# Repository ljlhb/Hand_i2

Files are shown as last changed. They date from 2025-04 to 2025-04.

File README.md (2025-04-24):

## 手i2

从图库下载 STL 文件：i2RightHand i2LeftHand。

在打印所有部件之前，您应该打印一份校准器 (CALIBRATOR)，以检查部件是否能够拼合。如果您在拼合这些部件时遇到困难，可以调整切片软件的水平扩展设置来解决这个问题。此设置可能因切片机和打印机而异，但用户报告称，将其设置为 -0.15 是一个不错的起点。

以下是一只右手所需的零件清单和打印数量：

1个i2_CoverFingerV3
1x i2_FingersMoldX5V3
1个 i2_FingersTipX5V2
1个i2_FingersX5V1
1x i2_HandCoverV1
1个i2_PalmCoverV2
1x i2_PulleyX5V1
1x i2_WristGearV1
1个 i2_WristLargeV2
打印腕部大件、手指模具、手指、腕带、滑轮，最大分辨率 0.25，填充率为 30%，壁厚为 2 毫米，无支撑，无筏。

打印 CoverFinger、FingersTip、HandCover、PalmCover，最大分辨率 0.25，填充率为 30%，壁厚为 2 毫米，需要支撑，如果打印机需要，则需要筏。

物料清单：

25个沉头螺钉M3 x 16mm
5 个 M3 x 4mm 沉头螺钉
1 个 M3 x 12mm 沉头螺钉
5 个平头螺钉 M1.5 x 4mm
5个膨胀弹簧3/16英寸x1-3/4或4.8毫米x44.5毫米
6x舵机 JX-6225MG 300度
1x 带状线 16 根 3 米
1 条编织鱼线 0.8 毫米 200 磅，3 米
5个霍尔传感器AH3503
5x 圆盘磁铁直径 2.5mmx1mm
1x 特氟龙管 ID1.5MM X OD2.5MM，3米

<h2>步骤1</h2>



将腕部伺服支架粘到 RobCableFront 上



用 4 个螺钉安装伺服电机



如果需要，用 M3 钻头重新钻孔



重新钻孔，以便 M3 PTFE 管穿过它们



使用 M3 钻头重新钻孔



将两个轴打印部件粘合在一起



检查以确保轴正确安装在两个印刷齿轮中



将 RobCableFront 和伺服支架安装到伺服床上



此视图向您展示了 WristGear 的组装以及各个部件如何组合在一起



将舵机角度设置为大约 90 度（HK15298B）或 150 度（JX-6225MG）。（即舵机总角度的中间值）。您可以使用此脚本(见脚本.txt)进行设置。用 3 毫米螺钉将组件末端安装到舵机轴上。



用 4 颗螺丝将组件拧到手腕上



按图示组装主齿轮



注意小齿轮的头部必须适合 RotaWrist2 的预留孔



使用 M3 螺丝刀将主齿轮与 RotaWrist3 对齐，然后添加 M3 x 12 毫米螺钉将它们固定在一起



删除那块打印的预支撑，你不再需要它了



用锋利的刀片，必要时清理边缘





使用 M8 钻头重新钻孔 WristLarge



使用 M3 丝锥，在将要固定手盖的地方准备一些 M3 x 16 毫米螺丝孔



使用 M3 丝锥，为安装弹簧的 M3 x 16 毫米螺钉准备孔



使用 M3 钻头，清理连接每个手指的所有孔



用M3钻头，将所有手指每3节的孔全部清理干净



用锋利的刀片清理霍尔传感器的出口



使用 M1.5 钻头，清理弹簧末端连接的孔



用填充物时，确保每个手指的三个部分都贴合，并且移动起来非常顺畅。这对于手指的良好功能至关重要。





使用 M5.5 钻头清理手指部分，让弹簧正常穿过



使用 M5.5 钻头清理手指部分，让弹簧正常穿过



这是为了向您展示如何将弹簧和三根传感器线安装在每个手指部分



确保针头可以穿过每个手指部分，如图所示，否则清理孔



使用 M3 x 16 毫米螺钉和螺栓将手指部分添加并安装在一起



确保编织鱼线的入口也清理干净



准备 5 条长度为 50 厘米的编织鱼线（0.8 毫米 200 磅）如果您在谷歌搜索中输入这些关键词，就可以找到该产品：编织鱼线 0.8 毫米 200 磅



准备一条40厘米长的带状电缆。你可以在谷歌搜索关键词：带状电缆 16 针（尽量选择最柔软、最细的）。



将丝带分成两部分，一部分长 40 厘米，有 6 根电线，另一部分长 10 根电线



从10根电线中完全移除1根电线。将9根电线分成三段，每段3根电线，长度均为15厘米。



用红色记号笔，给每个部分的一根电线涂上颜色。我们假设这些是正极 (+) 线



在丝带的两端都涂上这些颜色，这对于避免在进行最后的焊接时混合电线非常有用。



穿过腕部大号每 5 个丝带部分



将丝带穿过每个手指，注意不要倒着穿。另外要注意，每个手指的形状都差不多，只有拇指的形状不同。



现在把编织好的鱼线穿过每个手指。为了让鱼线末端更硬，可以加一些强力胶。



在 1 厘米长的编织钓鱼线上涂上强力胶。



等到它完全干燥后，从中间切开粘合部分，这样可以确保尖端坚固而纤薄。



通过将钓鱼线拉入指尖的 V 形凹槽，即可将其固定



现在将鱼线的另一端插入手腕大孔中



这是给你展示一下它应该是什么样子。我的照片上还没做拇指，不过你可以做。五个手指可以同时做。



如果你还没有这样做，请清理 3 毫米螺栓外壳，以便进行下一步



现在是时候添加 M3 x 16 毫米螺钉及其相应的螺栓，将手指组装到大腕上。从大拇指开始，然后是食指、无名指、小指，最后是拇指。



使用合适的 M8 印刷螺栓将 WristLarge 安装到 RotaWrist3



将微型夹具设置在打印螺栓的凹槽上



穿过主齿轮的最大丝带



然后穿过主齿轮第二条丝带



放置掌上盖并用 3 颗 M3 x 16 毫米螺钉固定



拧紧掌上盖时，确保将丝带整齐地放入凹槽中，并真正避免夹住它们



现在将 M2.5 PTFE 管穿过主齿轮特氟隆管 ID1.5MM X OD2.5MM PTFE 管的长度如下：拇指 335mm 食指 300mm 中间 300mm 无名指 300mm 小指 360mm

特氟隆管 ID1.5MM X OD2.5MM：https://fr.aliexpress.com/item/32730855848.html?spm=a2g0s.9042311.0.0.3b966c37jungcW



将管子穿过伺服底座孔。管子距离伺服轴约 1.5 厘米。



将鱼线穿过管子





并将管子的末端放入预留的孔中，直到无法再插入为止



对每根手指重复操作



现在获得 5 个弹簧弹簧 3/16″x1-3/4

弹簧 3/16″x1-3/4：https://www.ebay.com/p/19011685359



将一根鱼线穿过弹簧的一侧。鱼线总长度约为30厘米



将鱼线穿过主指部分的弹簧孔



将弹簧穿过第二个手指部分



取 5 个小螺丝，我用了一些安装在眼部机构中的伺服器上的螺丝，这些螺丝的直径约为 2 毫米





用钳子将螺丝剪至最大总长度为 4 毫米



将弹簧固定到位



装上那个小螺丝，把弹簧固定到位。确保螺丝没有刺穿三根带状电线



获取或切割五颗 3 毫米、最大长度为 4 毫米的螺钉



拉动鱼线，将弹簧头固定到位，然后安装螺丝。注意，我在螺丝刀上放了一块黑色磁铁，这样可以方便安装螺丝。



拧紧螺丝之前，先将鱼线拉出来



完成拧紧。确保没有刺穿三根带状电线



拿两根针



将手指的最后一部分最大限度地折叠起来，并将第一根针穿过手指和弹簧，直到它从另一侧出来。



折叠手指的第二节，并将第二根针穿过手指和弹簧，直至完全穿过。这样可以为每个手指节设置合适的张力。



用小钳子剪断针头



滴一滴强力胶，确保针头不会再出来



是时候用拇指做同样的事情了，只有两个手指部分，所以弹簧的张力较小，不需要针



拇指的另一个不同之处在于，我们将螺丝拧入盖子中，从而将弹簧固定到位。确保不要刺穿电线。虽然我的图片显示已经装好了拇指盖，但先不要装上，你仍然需要接触到内部。



让我们把霍尔传感器焊接到电线上。开始焊接中间的电线。注意传感器在图片上的位置，因为一侧是正极，另一侧是负极。霍尔传感器 AH3503

霍尔传感器 AH3503：https://fr.aliexpress.com/item/32899671134.html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





用一小块胶带保护焊锡。我用的是Kapton胶带。这部分操作比较精细。



焊接第二根和第三根电线并用胶带包裹起来



缠绕胶带时，胶带的厚度不应超过丝带本身的厚度，否则下一步将其推下去会很困难。



小心地将其推回指尖



这是指尖应该伸出的长度



你可以拉动手掌中的电线，帮助自己将霍尔传感器推回到尖端



将钓鱼线缠绕在凹槽周围，然后小心地将手指末端拧到传感器上。



注意，手指末端印有小螺纹，可以顺时针旋转至指尖。请勿用力过猛，否则螺纹会损坏。



完成每个手指的操作。



你可以用一些 16x3mm 的螺丝安装手指盖。虽然我的图片显示手指盖已经装好了，但先不要装，你仍然需要打开内部。



是时候把每根线焊接到 NervoBoard 的传感器板上了。拇指放在“0”上，食指放在“1”上，大拇指放在“2”上，无名指放在“3”上，小指放在“4”上。



您可以在此页面上查看有关传感器连接的更多信息：https://inmoov.fr/test-your-finger-sensor/



这里你可以看到我放置迷你模拟板的位置。你还可以在滑轮上看到，带小垫圈的螺丝是如何将鱼线用一个结固定住的。要做到这一点，你需要在你想要剪断鱼线的地方涂上一些胶水。



要做到这一点，你需要在你想要剪断的编织线上涂点胶水，让接触胶固化。胶水可以让剪断更容易。



然后，用锋利的剪刀剪掉涂有胶水的地方。



按照我在图中的方式拉动你的钓鱼线，它应该会形成一个大结。



拧紧结，将螺钉和垫圈放在结上，并在拧紧螺钉时保持结被拉住。



模具中有一个孔，用于插入直径为2毫米的部件，以便在模制硅胶中形成一个复位，以便磁铁复位。圆盘磁铁直径为2.5毫米x1毫米。

圆盘磁铁直径为2.5毫米x1毫米：https://www.supermagnete.fr/eng/disc-magnets-neodymium/disc-magnet-2.5mm-1mm_S-2.5-01-N52N



让它穿过2毫米。我使用了双组分透明RTV硅胶Ecoflex™ 00-10



用硅胶套件将每个指尖上的模制部件粘合起来



用指南针确定磁铁的南极。



将磁铁的南极朝向霍尔传感器，插入硅胶模制尖端的复位孔中。请使用木质牙签，因为任何金属工具都会粘在磁铁上。这项工作很精细，必须操作到位才能获得正确的结果。用一滴硅胶套装固定磁铁位置，并等待其干燥。使用此页面https://inmoov.fr/test-your-finger-sensor/测试您的传感器。

## 如何使用手指传感器

手指传感器可以用于各种功能。抓取鸡蛋或瓶子需要不同的压力。握手也需要检测施加的压力。触摸传感器有很多种实现方法，我做过两个版本，成本都非常低。带霍尔传感器的版本比原来的泡沫版本精确得多。

概括：

电子版（2 个版本）
设置
利用率

**带霍尔传感器的电子装置**

-此版本采用霍尔传感器和磁铁完成。

-当磁铁靠近霍尔传感器时，传感器会测量该值。

-该值被发送到模拟 Arduino 引脚。

-手部教程中解释了手指上传感器的组装。







**电子泡沫传感器**

- 手指传感器的原始版本是用 2 块铜板连接到一块防静电泡沫制成的。

-当泡沫被压缩时，两块铜板之间的电流流动更强。

-模拟 Arduino 引脚检测变化。

-手部教程中解释了手指上传感器的组装。





**设置**

打开 InMoov/config/ service_J_SensorFinger.config并进行如下设置。

[MAIN]

rightHandSensorActivated=True
rightHandSensorArduino=right

right_thumb_Psi_min=544当传感器未按下时，请在此处输入最大值。
right_thumb_Psi_low=545一般情况下，取最小值，如果使用 AH3503 霍尔传感器，则加 1。
right_thumb_Psi_mid=547一般情况下，取最小值，加 4。
right_thumb_Psi_max=550一般情况下，取最小值，加 7。

right_index_Psi_min=538
right_index_Psi_low=539
right_index_Psi_mid=542
right_index_Psi_max=545

添加每个手指传感器的值……

要检查手指传感器是否工作正常并查看其值，您可以在 Python 窗口中输入并执行：

sensorTimerStart()

并在 python 选项卡中查看结果。

您可以使用以下方法关闭传感器定时器：

sensorTimerStop()

**利用率**

<h2>我们有三个选择：</h2>

1-如果您已经设置了传感器配置文件，某些手势将自动使用传感器。

2-直接在 Arduino 上使用代码进行测试。

3-使用 MyRobotLab 中的 Python 代码进行测试。（如果您没有运行 START_INMOOV）

<h3>第一个选项：</h3>

shakehands()当手闭合时，手势将自动使用传感器。

您可以将手势所需的压力调整为 0 到 3 之间的值。当传感器达到所需压力时，手指伺服器将停止其位置并禁用。

if rightHandSensorActivated:
    rightHandSensorON()
    sleep(1.5)
    rightThumbPressure=1 # Pressure range between 0-3
    rightIndexPressure=1
    rightMajeurePressure=1
    rightRingFingerPressure=1
    rightPinkyPressure=1
    i01.rightHand.moveTo(79,170,180,180,180,180)
    sleep(2)
    rightHandSensorOFF()
else:
  i01.rightHand.moveTo(79,90,140,130,122,180)

<h3>第二种选择：</h3>

-将此代码上传到您的 Arduino 板：

// A small script to test one servo and one sensor.

// Connect one sensor cable to the PIN A0, and the other cable
// to the 5V of your Arduino.
// The servo will be connected to your power supply (Gnd,Vcc)
// and to the PIN 2 of your Arduino.
// Set the serial of your Arduino at 57600 in device manager
// More detail on connection here https://inmoov.fr/test-your-finger-sensor
    
#include <Servo.h>

const int servoPin = 2;
const int sensorPin = A0;
int sensorReading;

int position;

Servo myservo;

void setup(){
  Serial.begin(57600);
  myservo.write(30);  // Closed claw.
  position = 30;
  myservo.attach(servoPin );
}

void loop(){
  sensorReading = analogRead(sensorPin);
    Serial.print("Analog reading = ");
    Serial.print(sensorReading); // the raw analog reading
    // We'll have a few threshholds, qualitatively determined
    if (sensorReading < 25) {
    Serial.println(" - No pressure");
    } else if (sensorReading < 30) {
    Serial.println(" - Light touch");
    } else if (sensorReading < 50) {
    Serial.println(" - Light squeeze");
    } else if (sensorReading < 110) {
    Serial.println(" - Medium squeeze");
    } else if (sensorReading < 200) {
    Serial.println(" - Big squeeze");
    }
    delay(1000);
  openClaw();
  delay(3000);
  closeClaw();
  delay(3000);
}

void openClaw() {
  for (; position < 130;  position++) {
    myservo.write(position);
    if(analogRead(sensorPin) > 30)
      break;
  }
}

void closeClaw() {
  myservo.write(30);  // Go to open position
  position = 30;
}

- 连接传感器（以 FSR 传感器为例）和伺服电机。有些伺服电机需要的电流过大，无法直接由 Arduino 供电。如果您的伺服电机抖动或运动不稳定，请为伺服电机连接一个额外的电源，并确保将 Arduino 连接到该额外的电源，如下所示：



-当通电时，手指会自动缓慢闭合，如果传感器检测到压力，则会在 Arduino.exe 监视器中显示信息。

-您可能需要更改代码中的传感器值以达到更好的调整。

为此，请检查监视器上的结果并根据需要直接在代码中更改这些值：

(sensorReading < 25)
(sensorReading < 30)
(sensorReading < 50)
(sensorReading < 110)
(sensorReading < 200)

<h3>第三种选择：</h3>

这里我们假设您已经安装了 MyRobotLab 并且知道如何使用它，如果没有，请先转到此页面。

-双击 MRL 目录中的“myrobotlab.jar”启动 MyRobotLab。

-按照第一个选项教程中的图像，在 Arduino 和伺服电机之间建立相同的连接。

-将此 python 脚本复制并粘贴到 MyRobotLab 中的 python 选项卡。

#这个简单的传感器 InMoov 脚本在 MyRobotLab 版本 1.0.2693 上进行了测试
#可以通过 Oscope 和手指动作看到结果。
#将一根传感器电缆连接到 PIN A0，将另一根电缆连接到 Arduino 的 5V。
#Servo 将连接到 Arduino 的引脚 2。
#根据您的Arduino板更改代码中的COM端口。

leftPort = "COM10"

Voice="US-English_Matthew"
mouth = Runtime.createAndStart("i01.mouth", "NaturalReaderSpeech")
#mouth.installComponentsAcceptLicense(Voice)
mouth.setVoice(Voice)
mouth.setRate(-10)

i01 = Runtime.createAndStart("i01", "InMoov")
i01.startMouth()
leftHand = Runtime.create("i01.leftHand","InMoovHand")
i01.startLeftHand(leftPort)
i01.leftHand.index.map(0,180,25,165)

left=Runtime.create("i01.left", "Arduino")
left.setBoard("atmega2560")
left = Runtime.start("i01.left", "Arduino")
left.connect("COM10")

def publishPin(pins): 
    for pin in range(0, len(pins)):
        print pins[pin].address, pins[pin].value
        if pins[pin].value<=540:
          print "No pressure"
        if pins[pin].value>=541 and pins[pin].value<=542:
          print "Low pressure"
        if pins[pin].value>=543 and pins[pin].value<=544:
          print "Soft pressure"
          FingerGoesBack()
        if pins[pin].value>=545:
          print "High pressure"
          FingerGoesBack()
          i01.mouth.speak(u"OUCH, that hurts") 
 
left.addListener("publishPinArray","python","publishPin")
sleep(5)
left.enablePin(54,1) # 54 is pin A0, Number 1 is how many polls/second

i01.leftHand.setAutoDisable(True)

def moveFingerSlowly():
    i01.leftHand.index.enable()
    i01.leftHand.index.setVelocity(25)
    sleep(2)
    i01.leftHand.index.moveTo(180)

def FingerGoesBack():
    i01.leftHand.index.enable()
    i01.leftHand.index.setVelocity(-1)
    i01.leftHand.index.moveTo(0)
 
#此简单的 InMoov 传感器脚本已在 MyRobotLab 1.1.812 版本上测试。
#结果可在 Oscope 中通过手指动作查看。
#将一根传感器线缆连接到 Arduino 的 A0 引脚，另一根线缆连接到 Arduino 的 5V 接口。
#伺服器将连接到 Arduino 的 2 引脚。
#根据您的 Arduino 开发板更改代码中的 COM 端口。

Voice="Mark" 
i01_mouth = Runtime.start("i01.mouth", "MarySpeech") 
#i01_mouth.installComponentsAcceptLicense(Voice) 
i01_mouth.setVoice(Voice) 

i01_left=Runtime.create("i01.left", "Arduino") 
i01_left.setBoard("atmega2560") 
i01_left = Runtime.start("i01.left", "Arduino") 
i01_left.connect("COM3") 

i01 = Runtime.start("i01", "InMoov2") 
i01.startMouth() 
i01_leftHand = Runtime.start("i01.leftHand","InMoov2Hand") 
i01_leftHand_index.map(0.0,180.0,0.0,180.0) 
i01_left.attach("i01.leftHand") 

def publishPin(pins):
    对于范围内的引脚（0，len（pins））：
        打印 pins[pin].address，pins[pin].value
        如果 pins[pin].value<=540：
          打印“无压力”
        如果 pins[pin].value>=541 且 pins[pin].value<=542：
          打印“低压”
        如果 pins[pin].value>=543 且 pins[pin].value<=544：
          打印“轻压” 
          FingerGoesBack()
        如果 pins[pin].value>=545：
          打印“高压” 
          FingerGoesBack() 
          i01.mouth.speak(u“哎哟，好疼”）
 
i01_left.addListener("publishPinArray","python","publishPin") 
sleep(5) 
i01_left.enablePin(54,1) # 54 是引脚 A0，数字 1 是每秒轮询次数

i01_leftHand.setAutoDisable(True) 

def moveFingerSlowly（）：
    i01_leftHand_index.enable（）
    i01_leftHand_index.setSpeed（25）
    睡眠（2）
    i01_leftHand_index.moveTo（180）

def FingerGoesBack（）：
    i01_leftHand_index.enable（）
    i01_leftHand_index.setSpeedy（250）
    i01_leftHand_index.moveTo（0）

-当通电时，手指会自动缓慢闭合，如果传感器检测到压力，它会在 Python 监视器中显示信息，并停止闭合并说出与他感受到的压力相关的内容。

-您可能需要更改代码中的传感器值以达到更好的调整。

为此，请检查监视器上的结果并根据需要直接在代码中更改这些值：

value<=540
value>=541
value<=542
value>=543
value<=544
value>=545

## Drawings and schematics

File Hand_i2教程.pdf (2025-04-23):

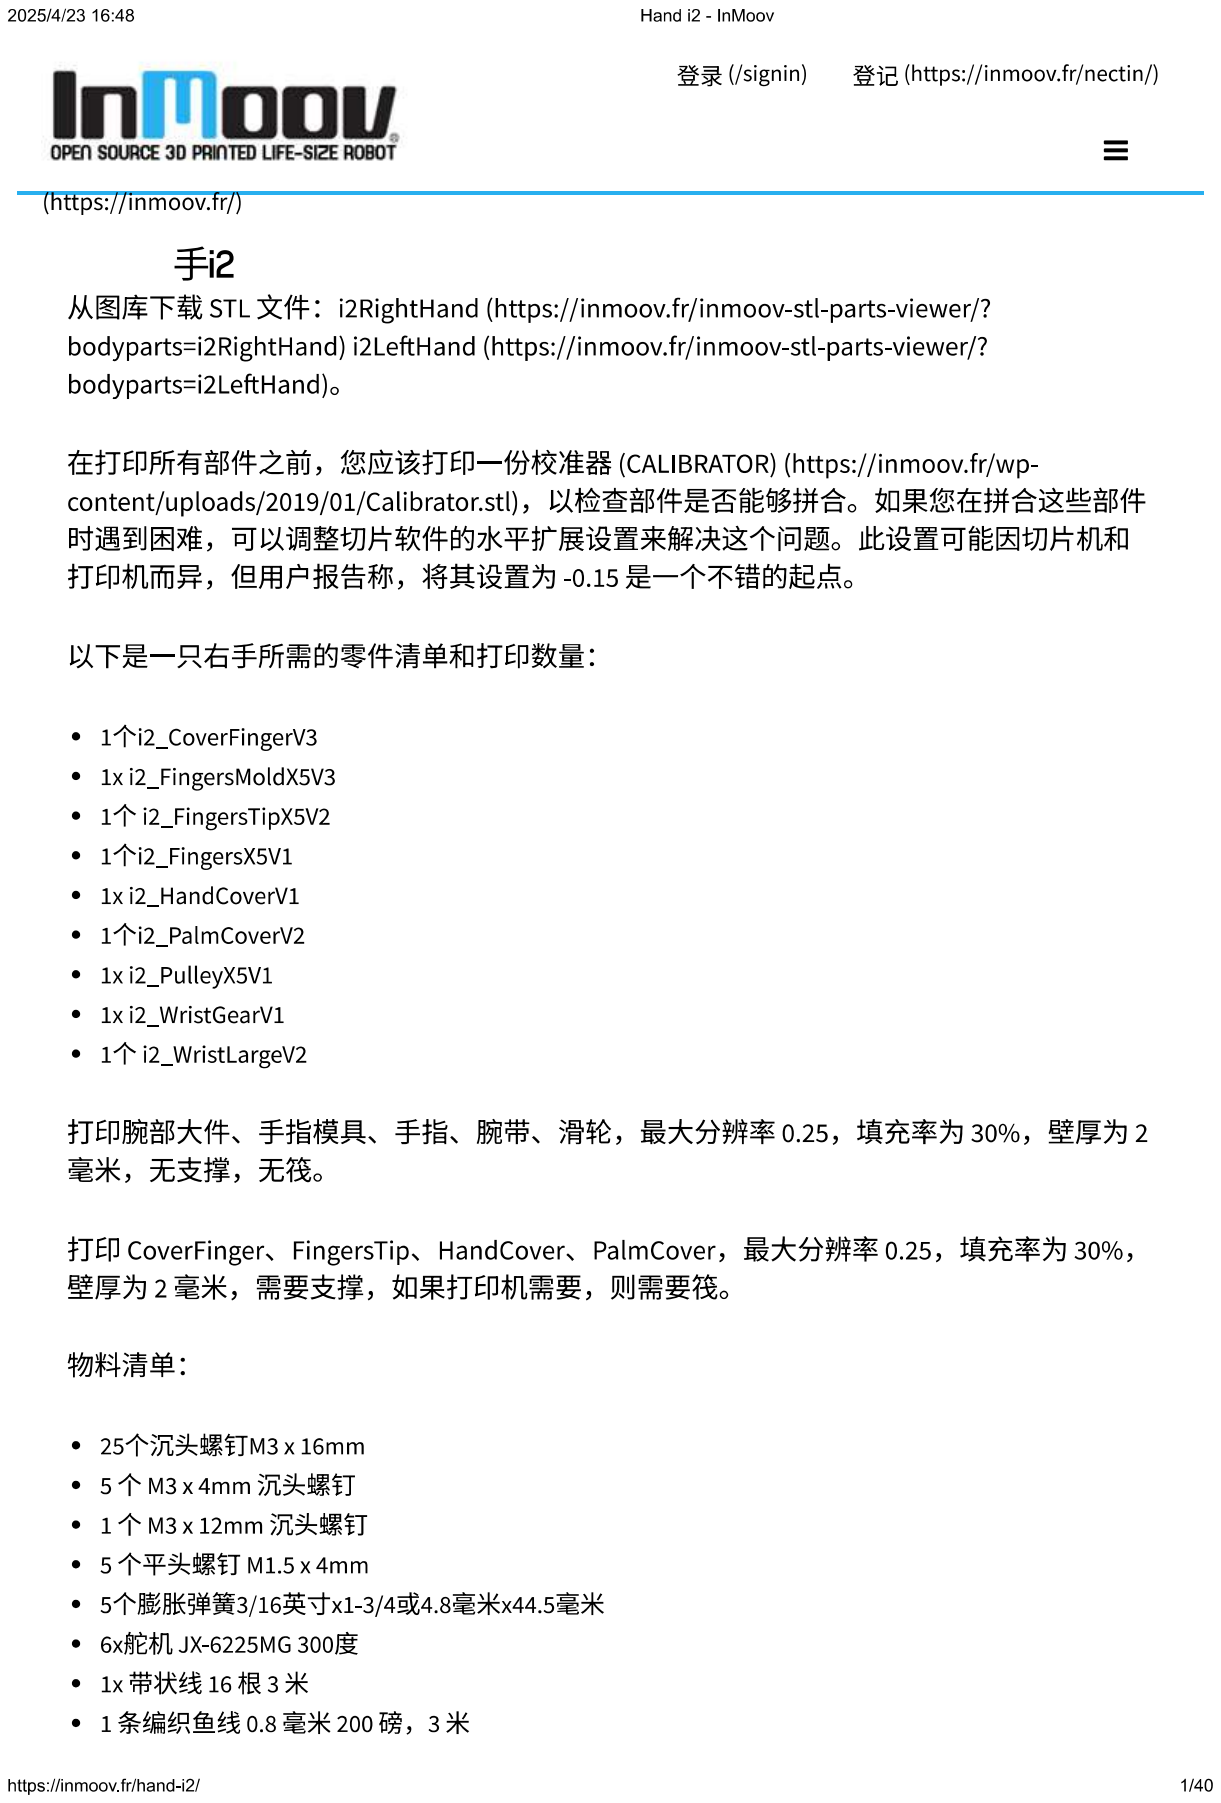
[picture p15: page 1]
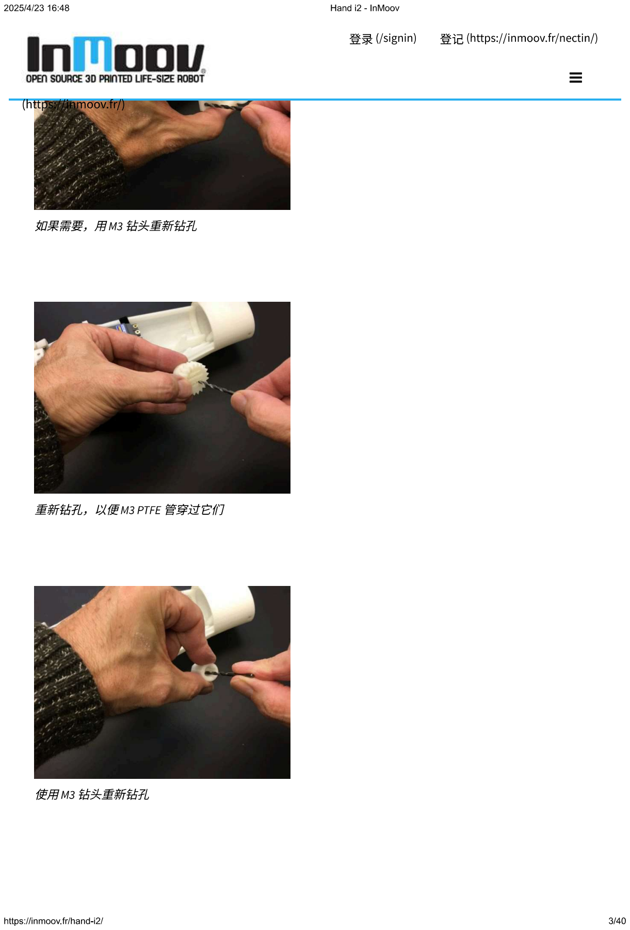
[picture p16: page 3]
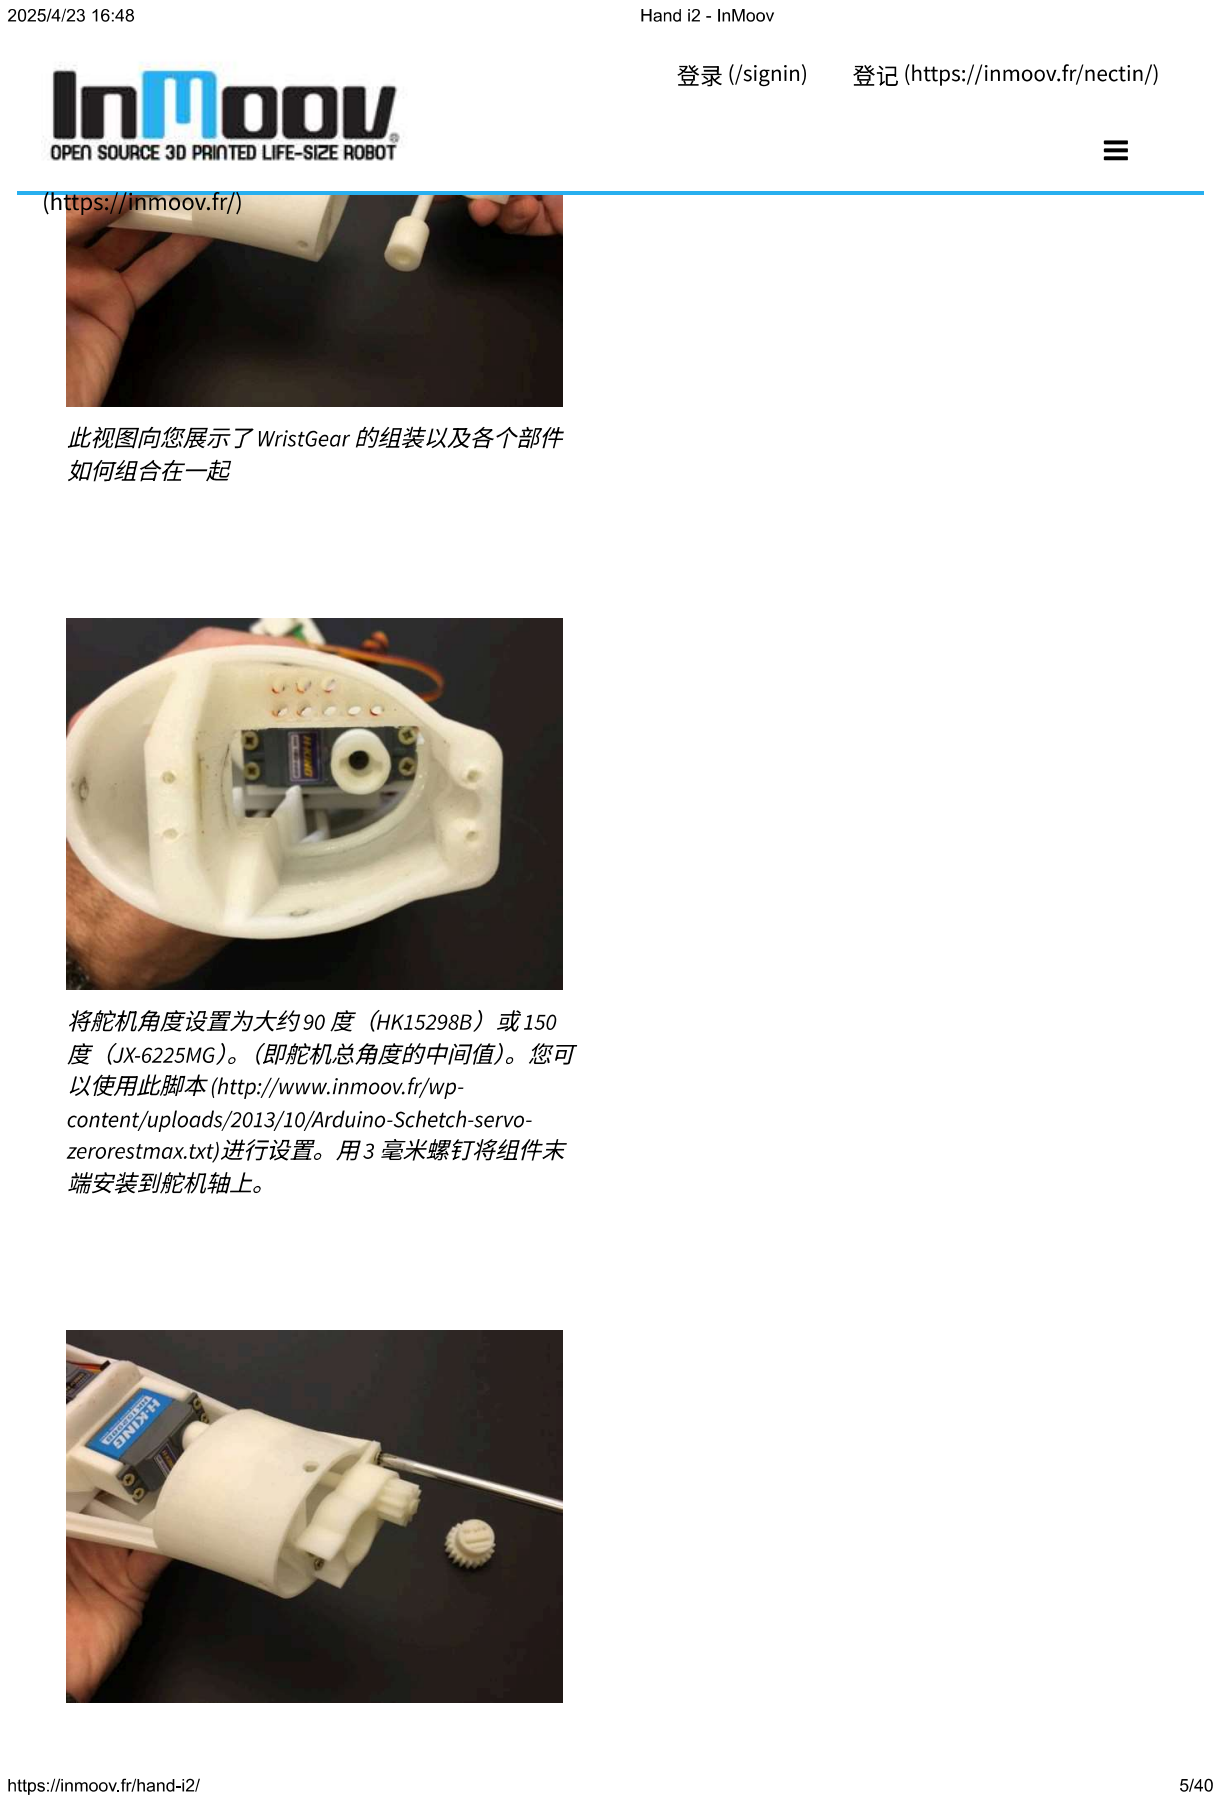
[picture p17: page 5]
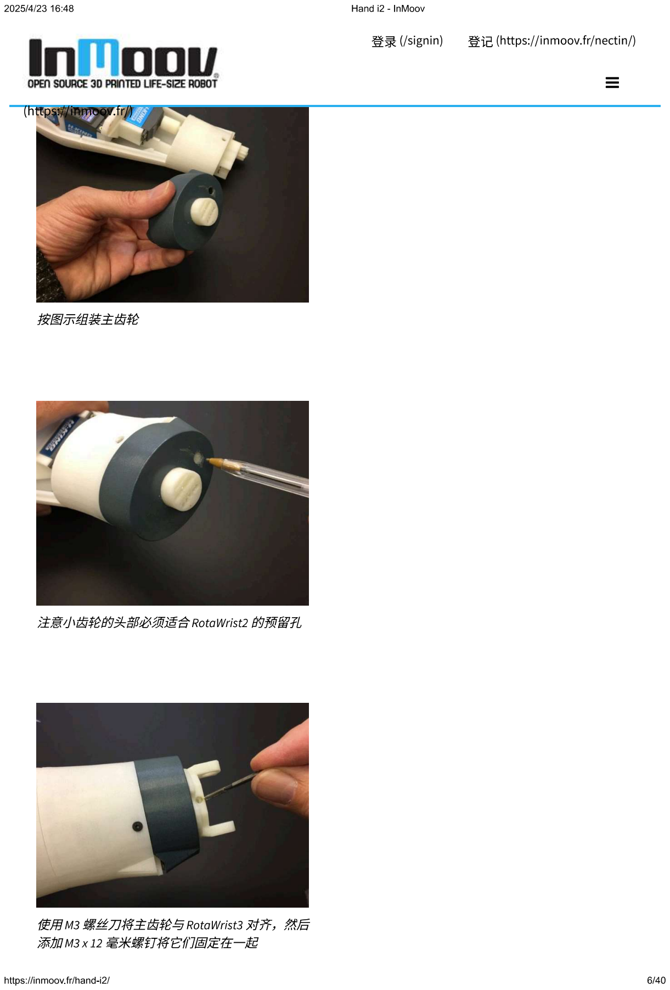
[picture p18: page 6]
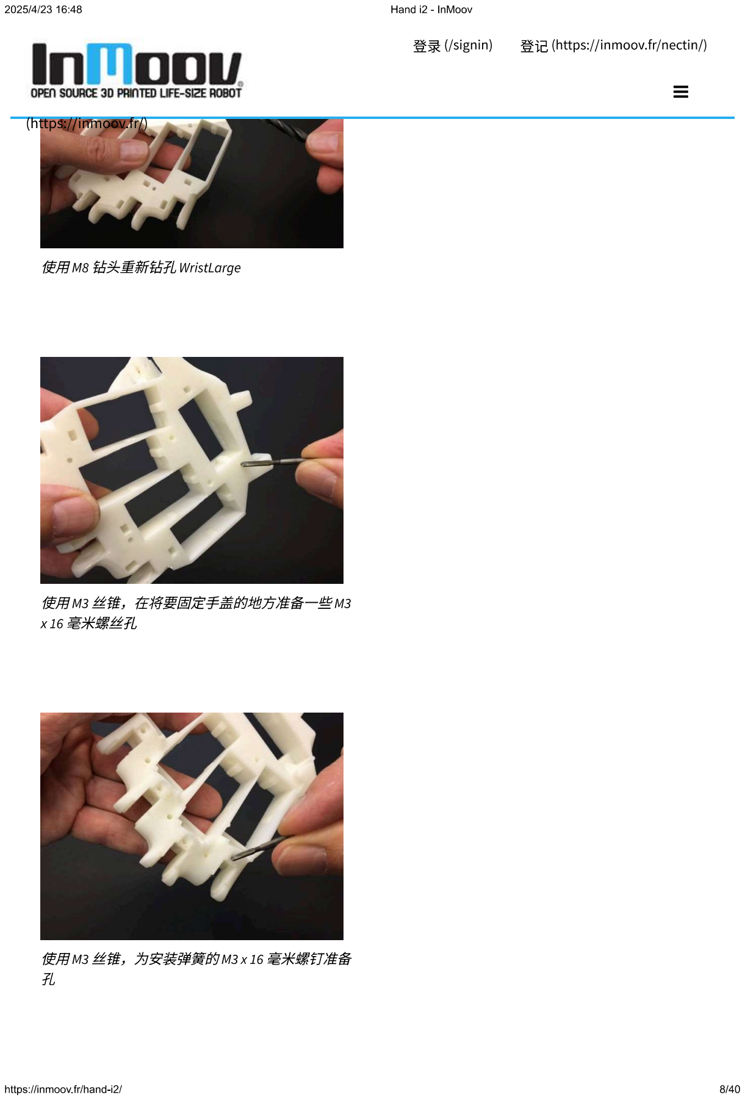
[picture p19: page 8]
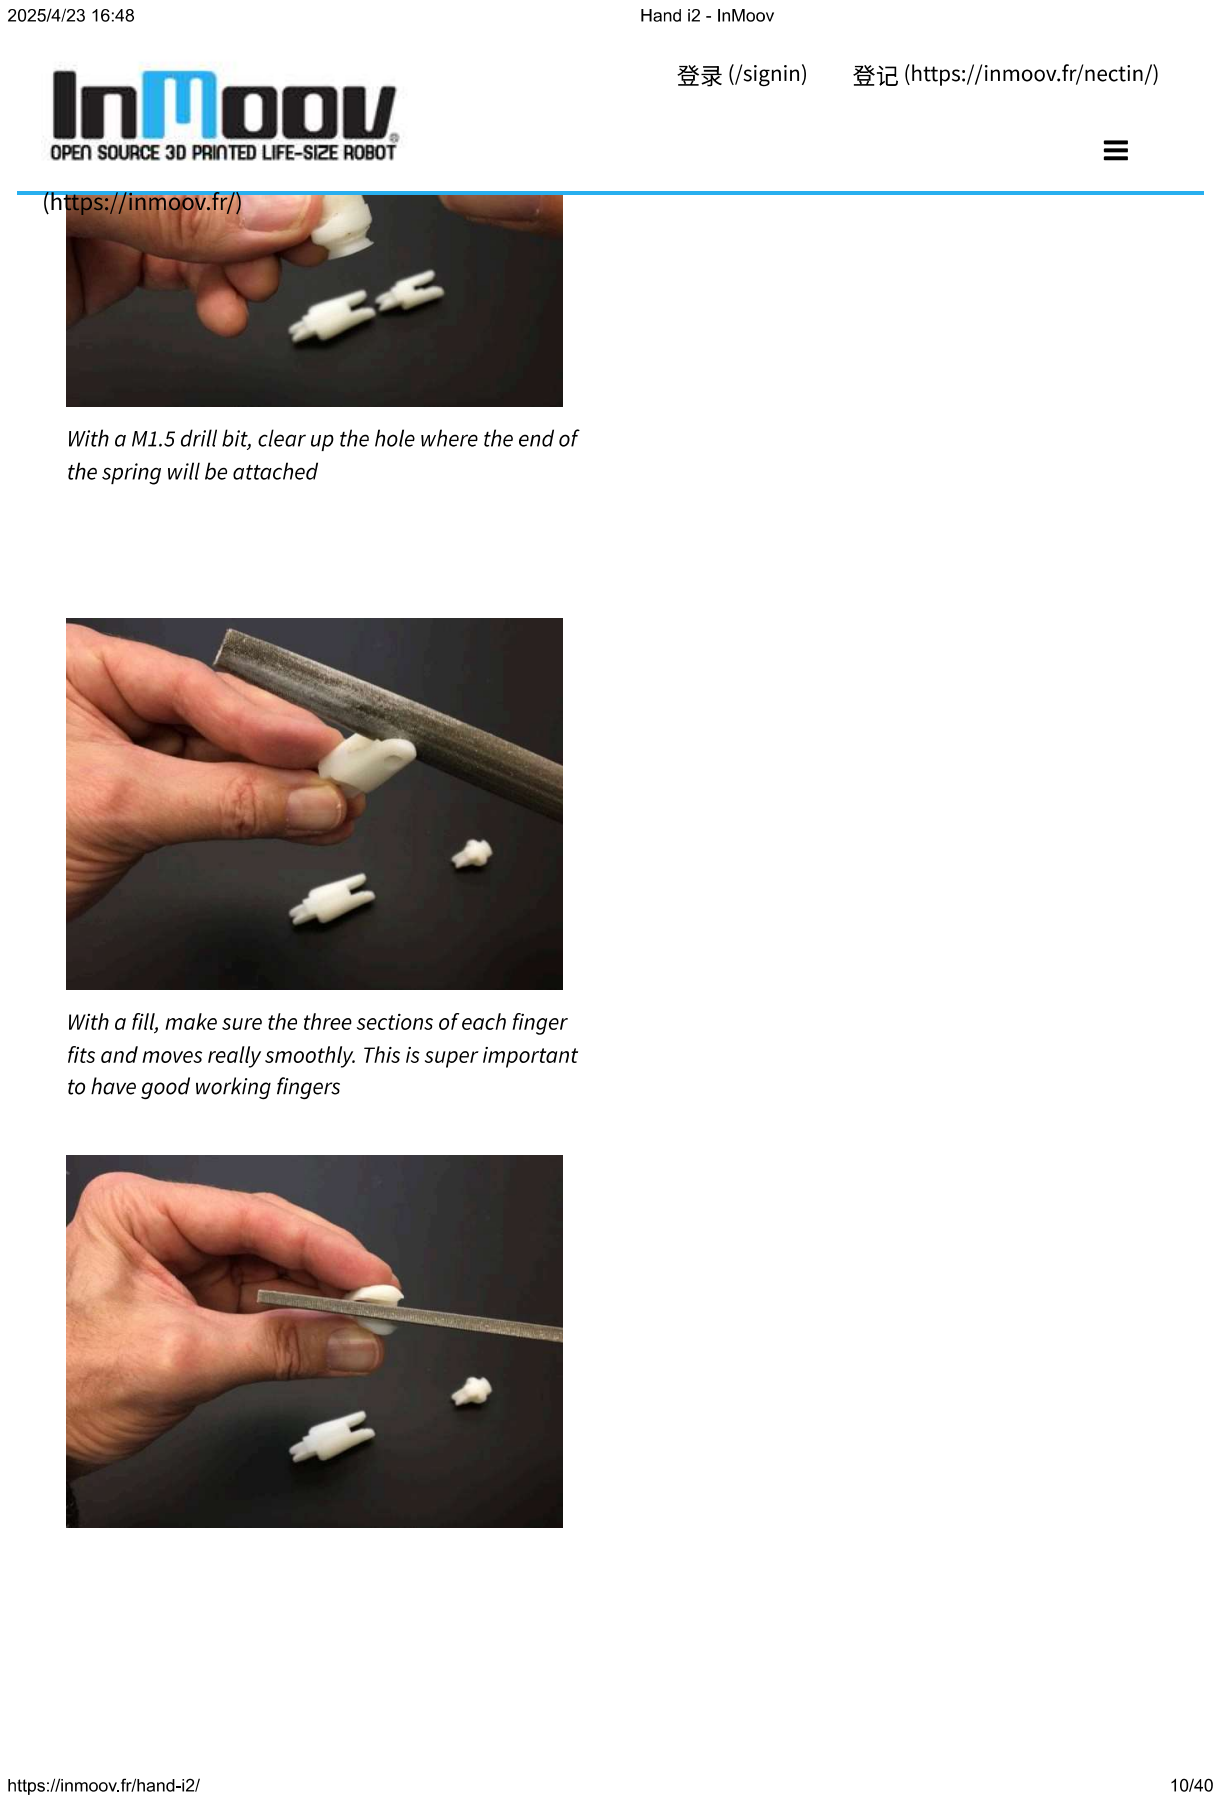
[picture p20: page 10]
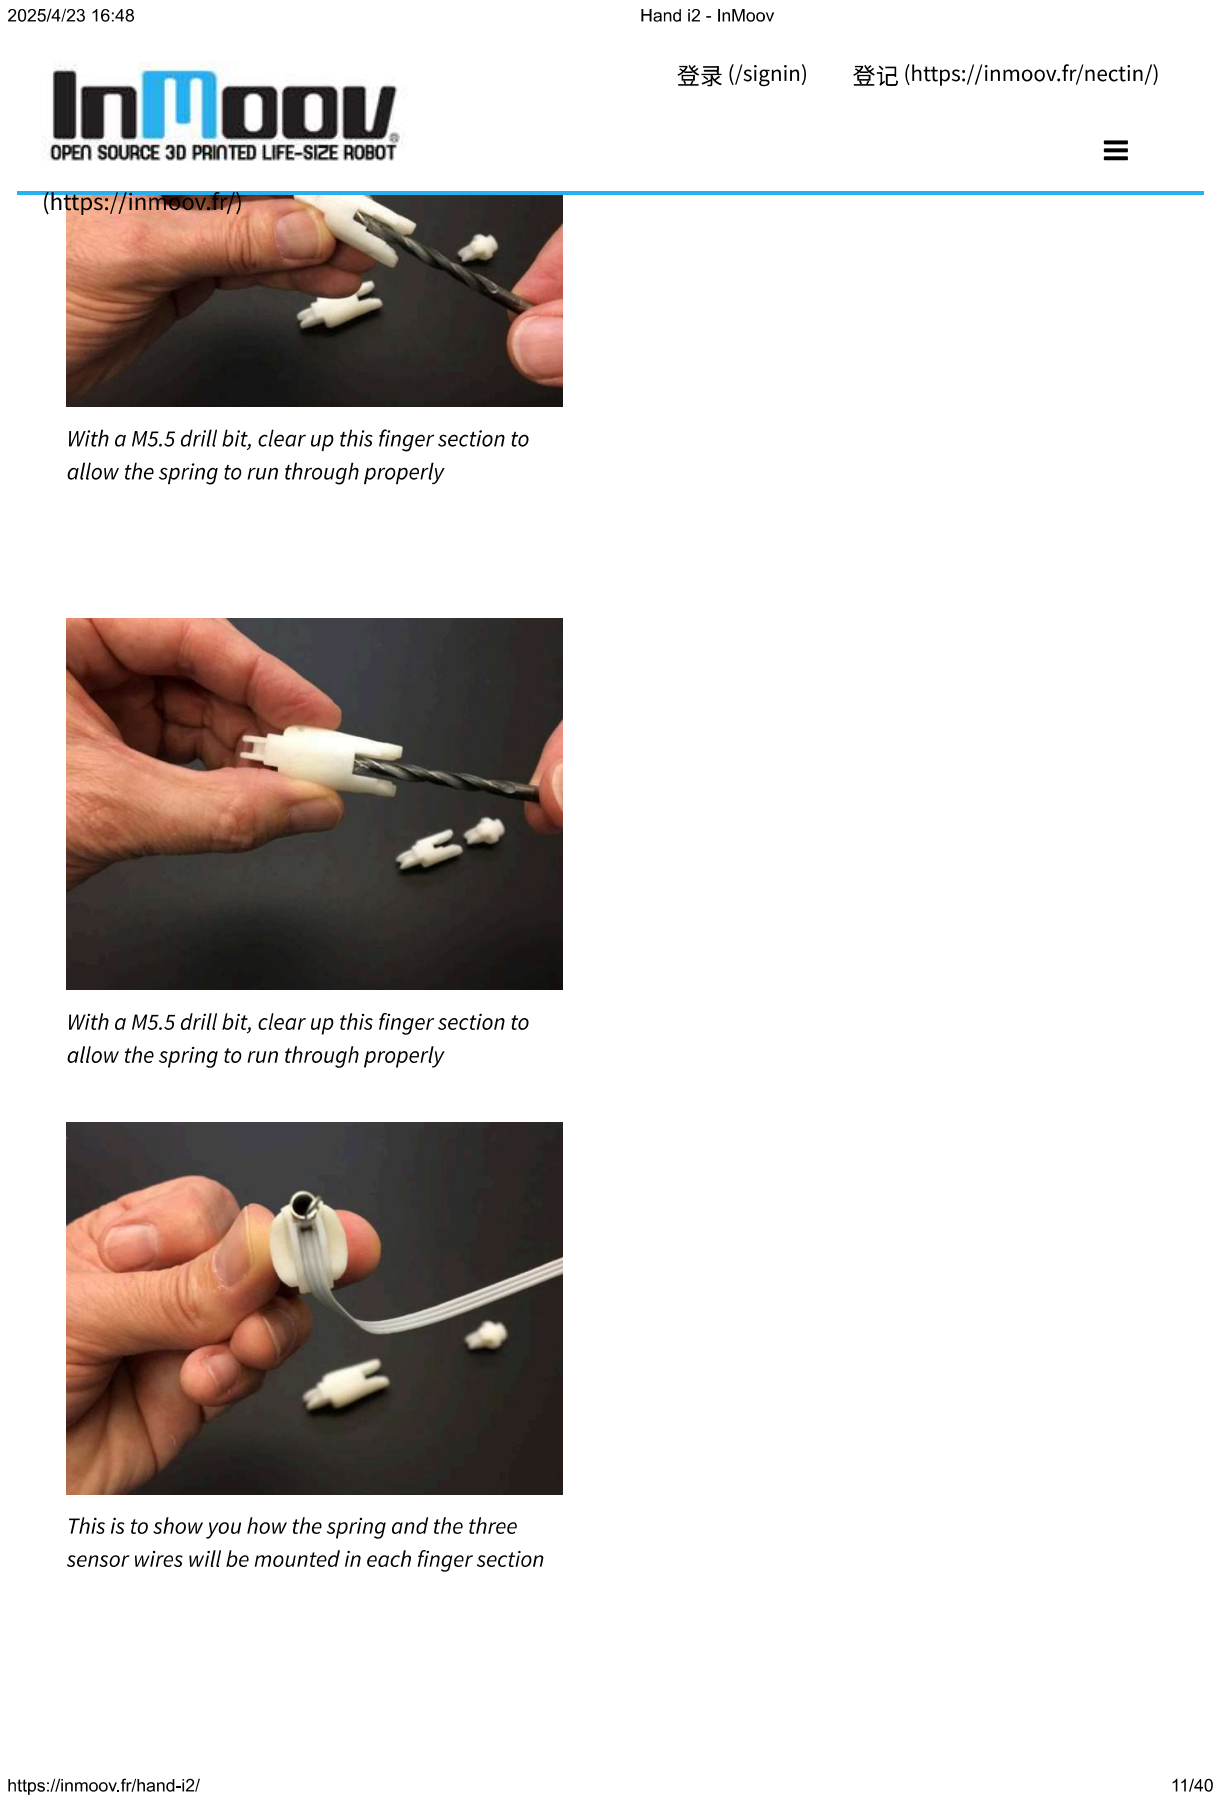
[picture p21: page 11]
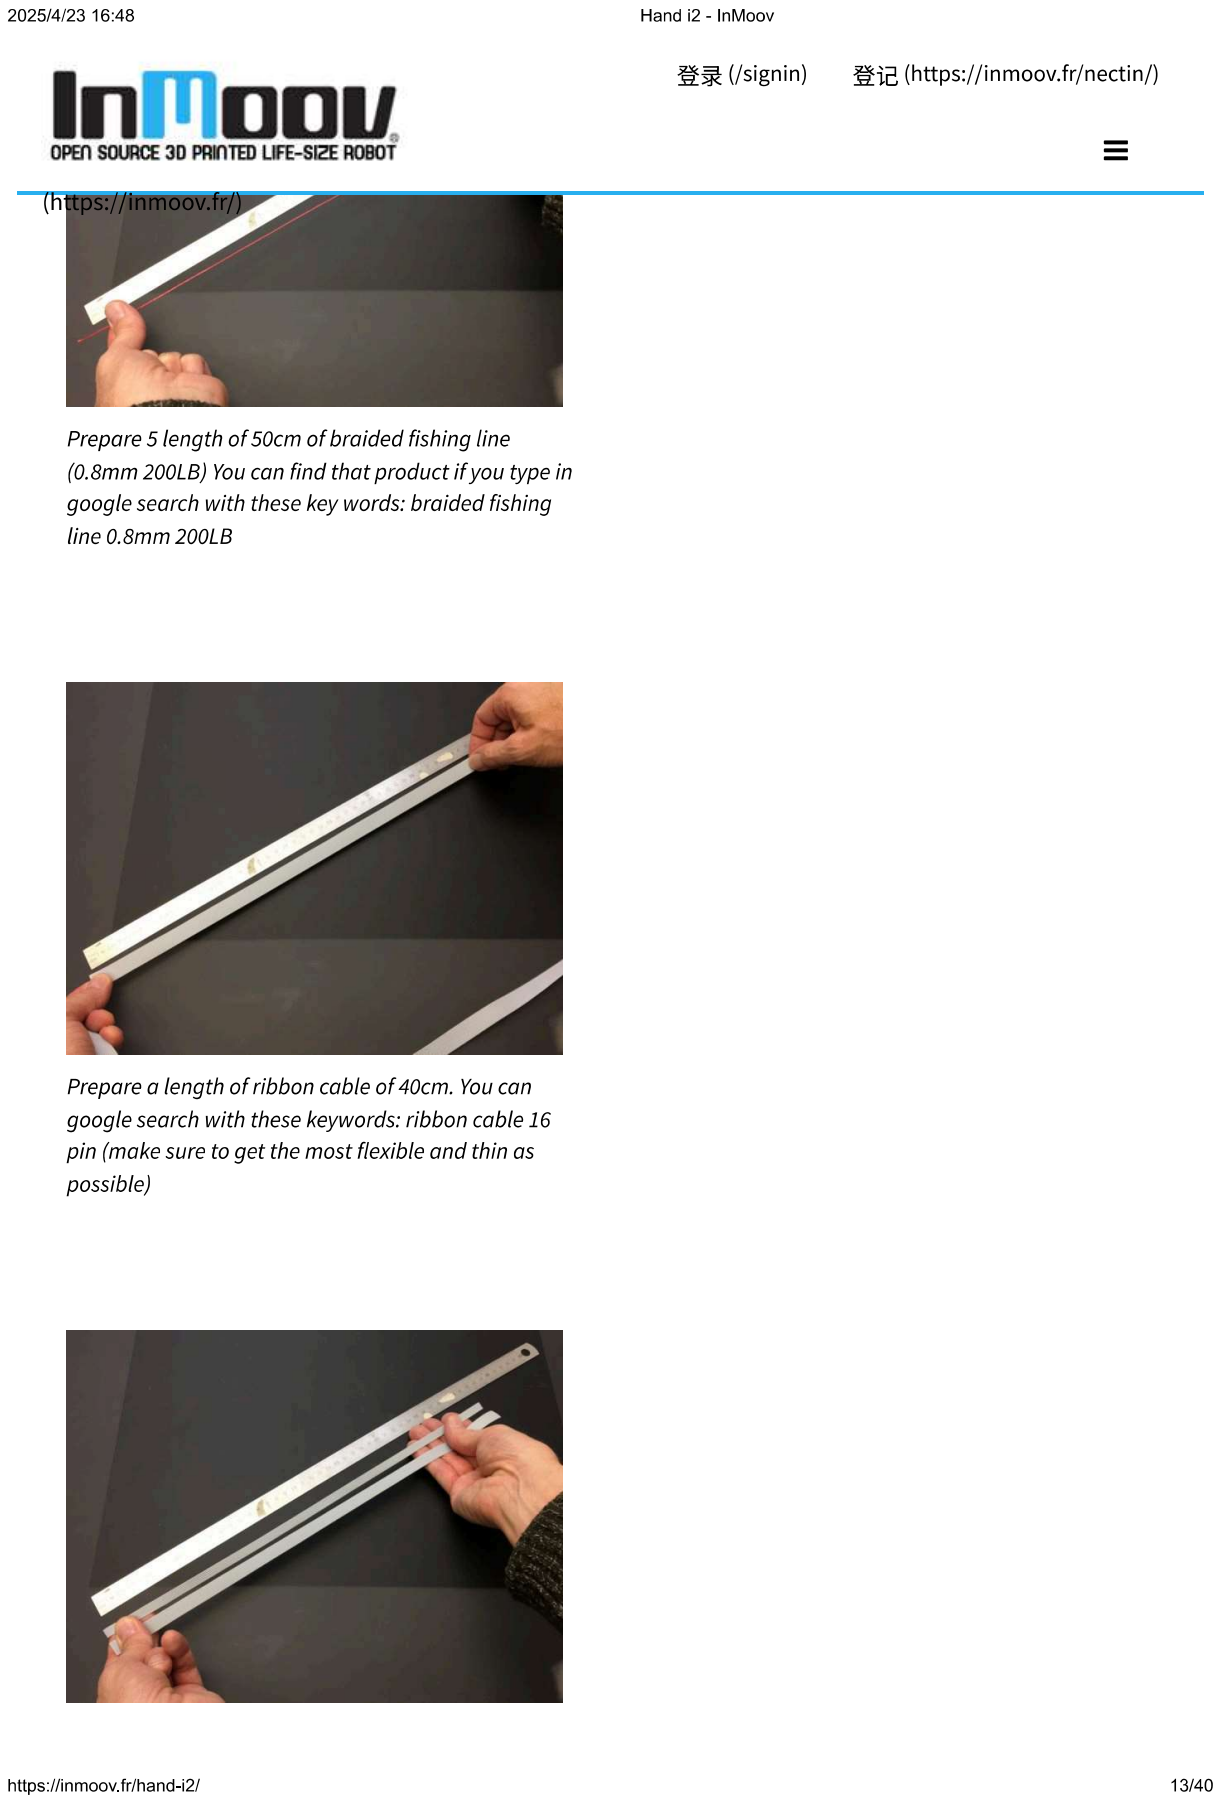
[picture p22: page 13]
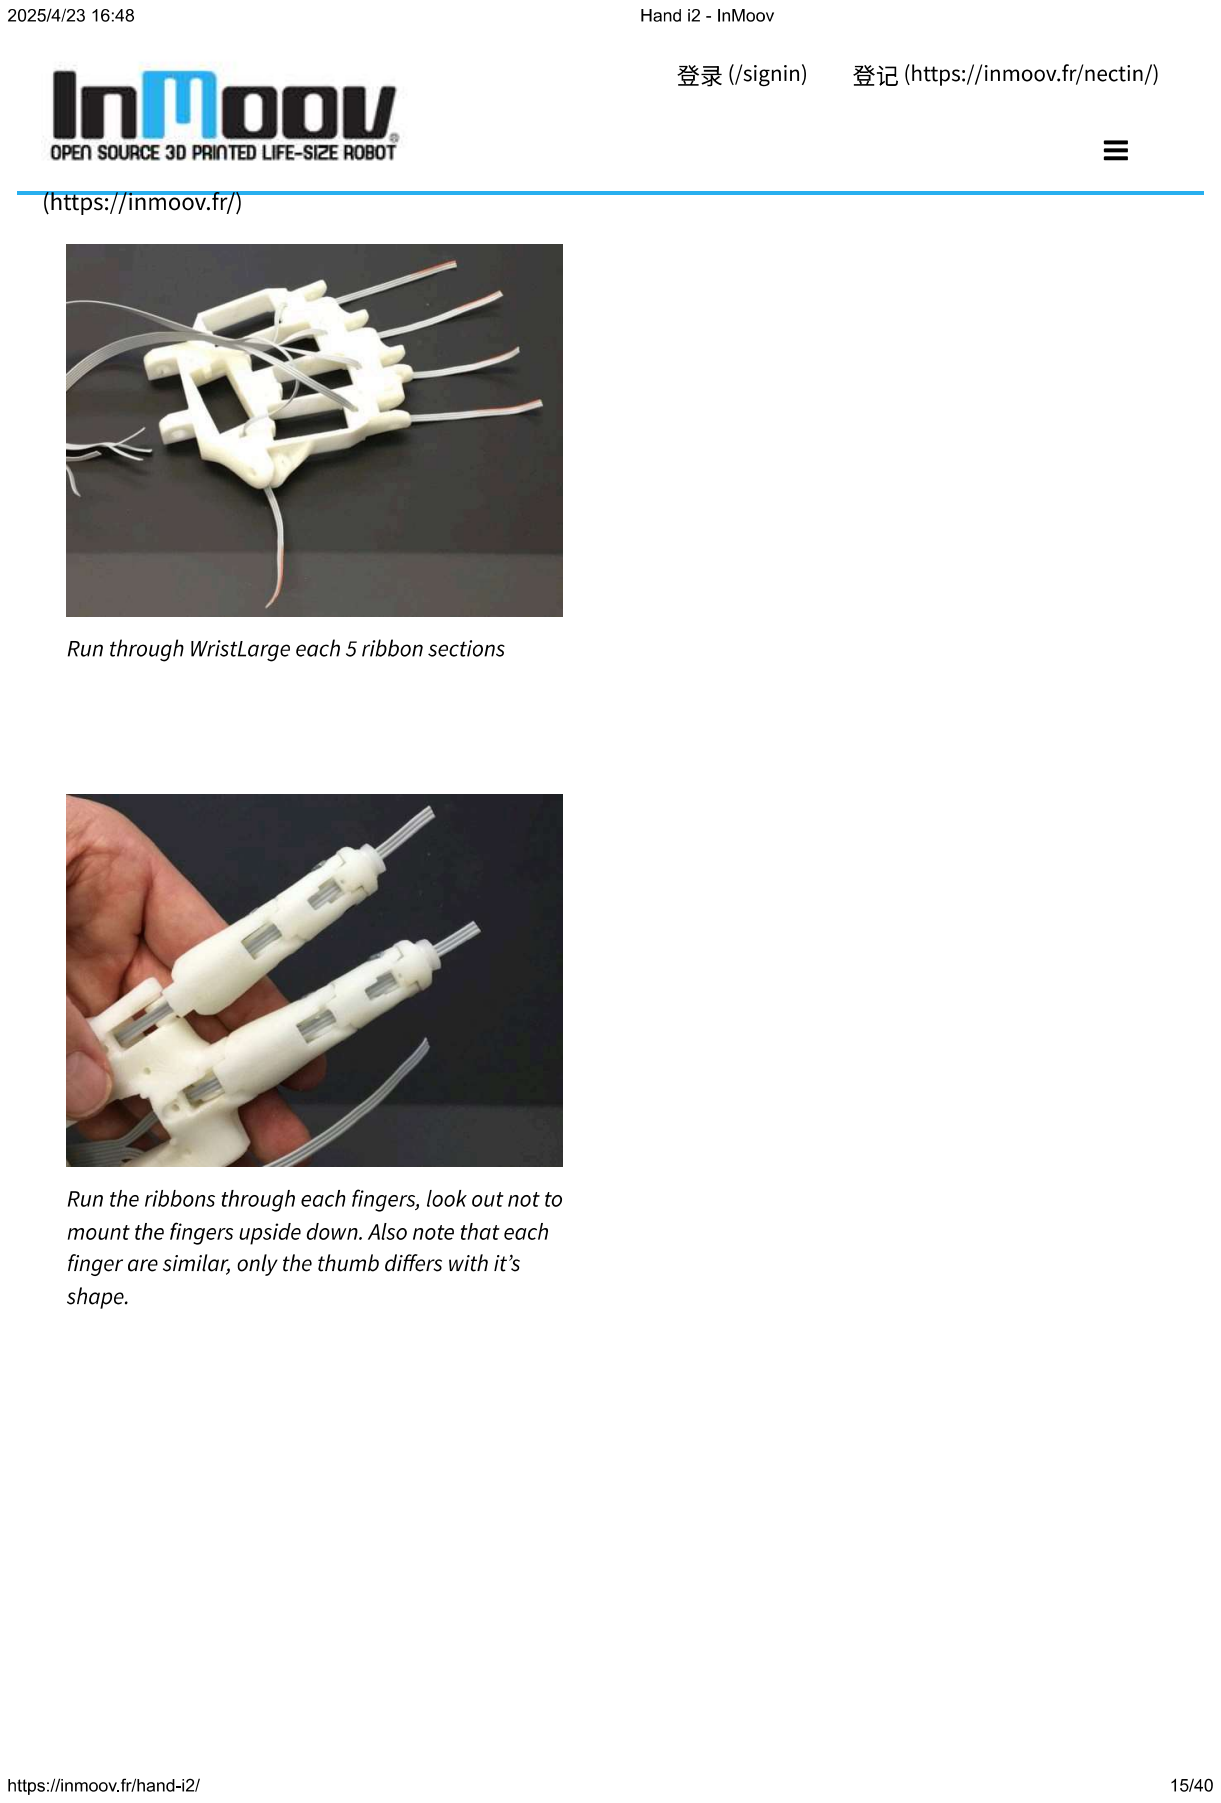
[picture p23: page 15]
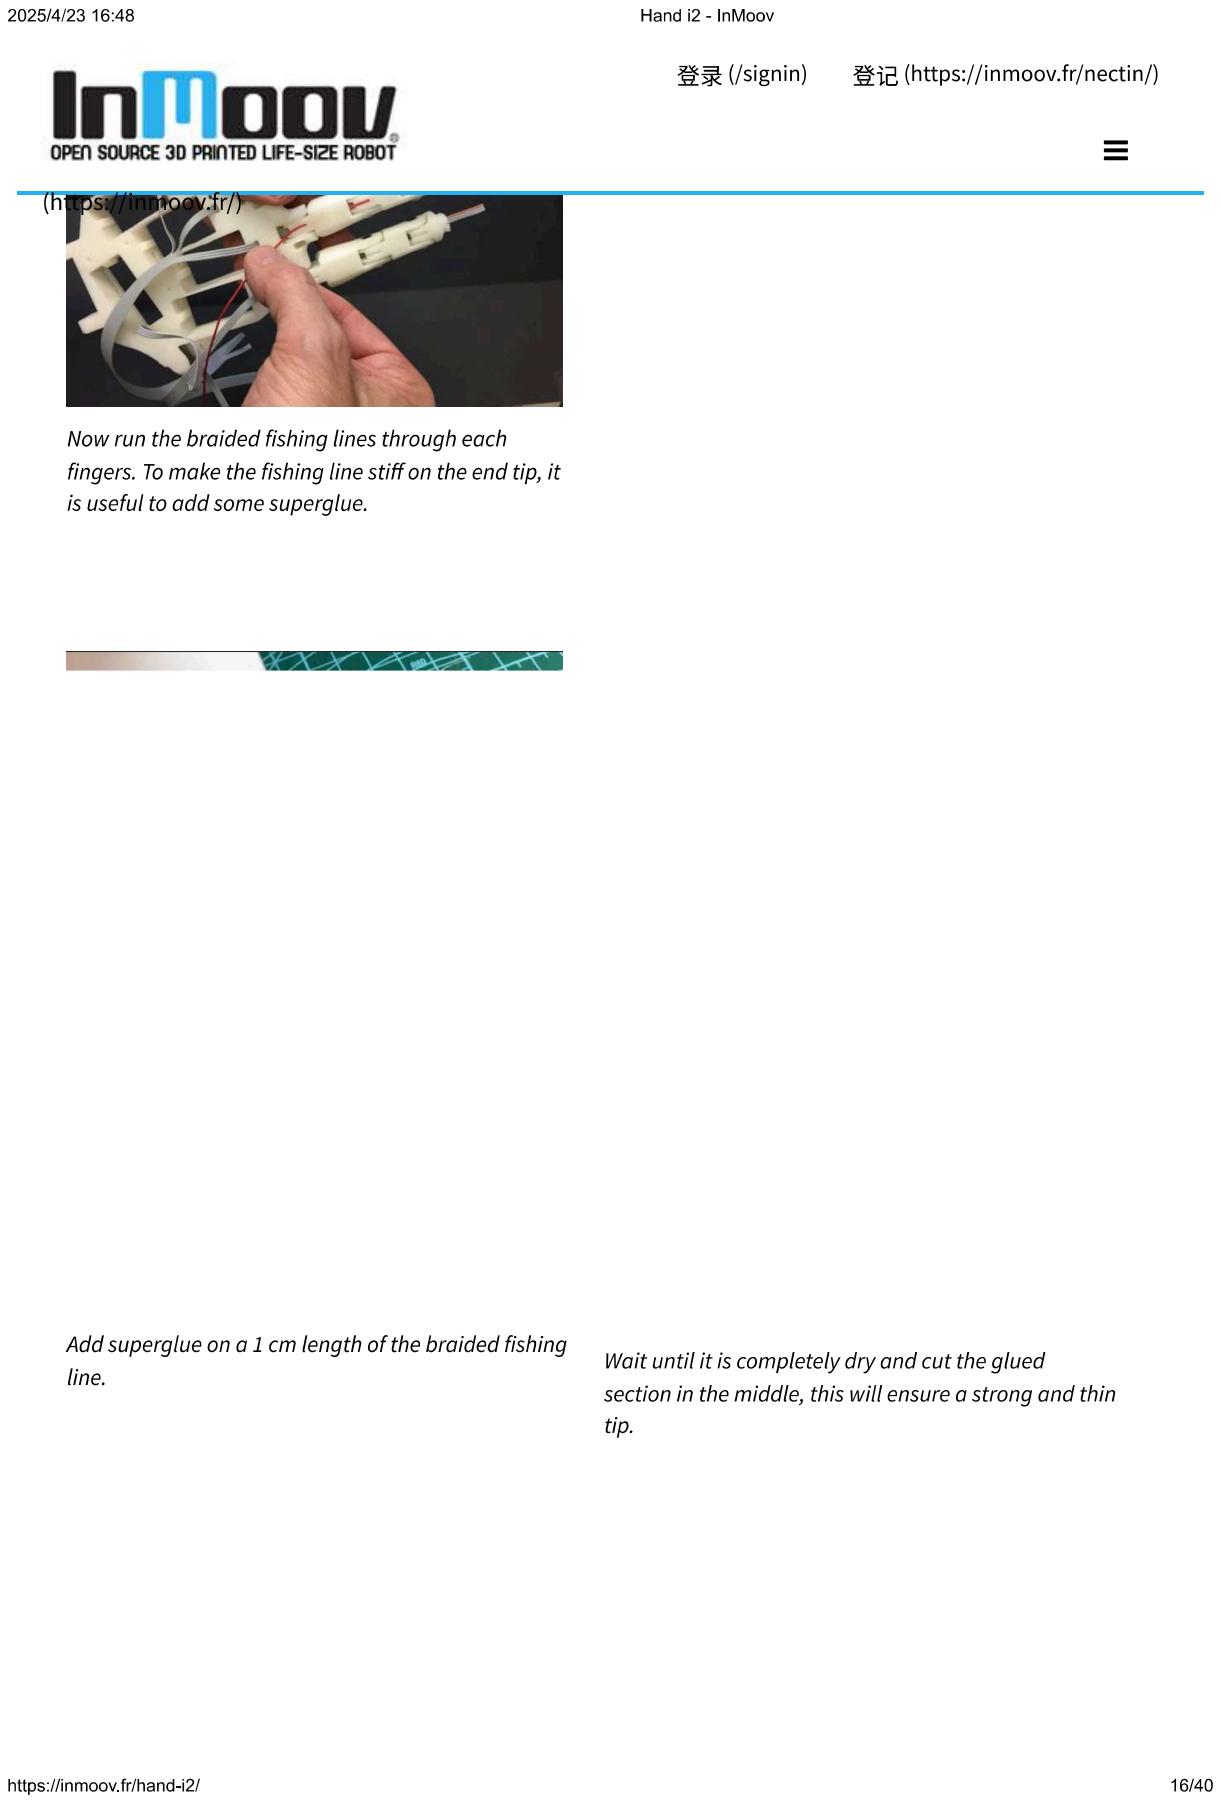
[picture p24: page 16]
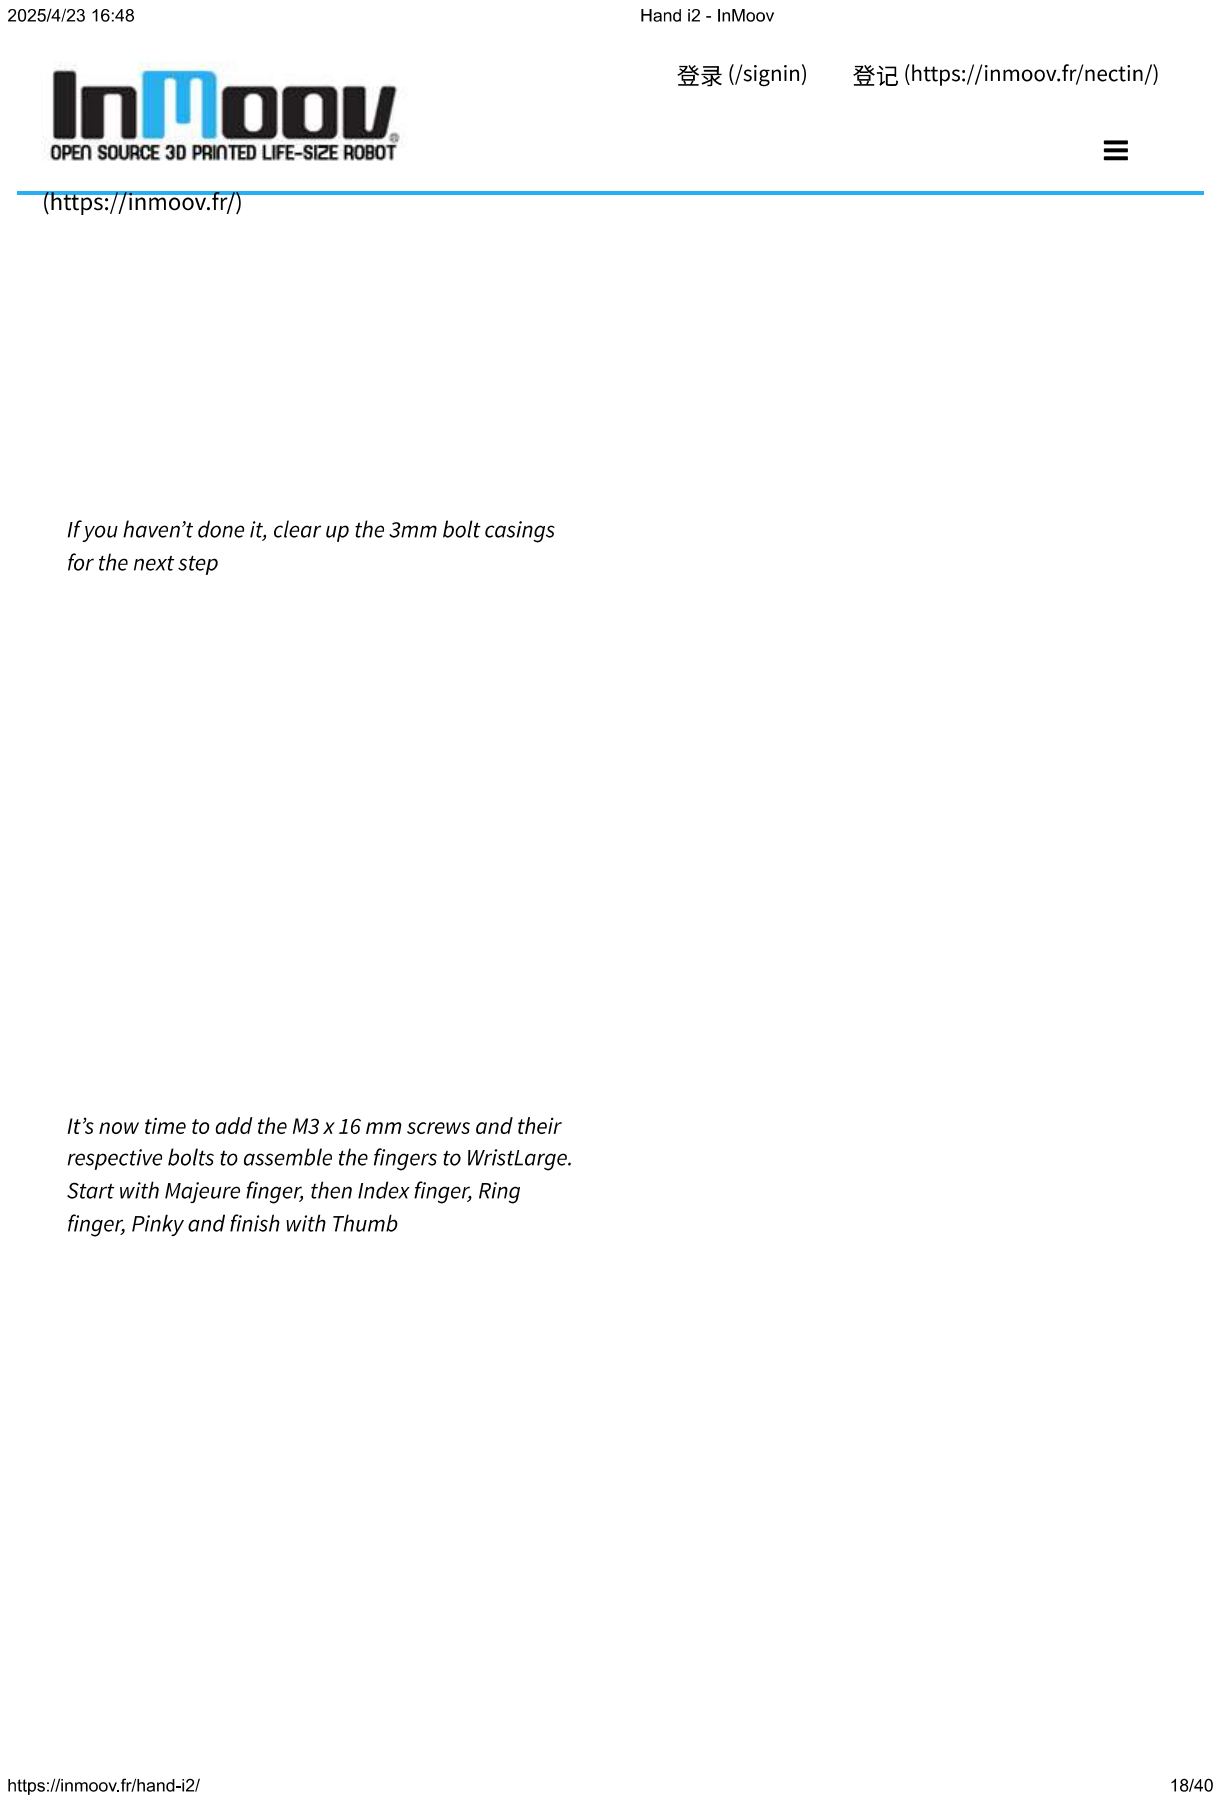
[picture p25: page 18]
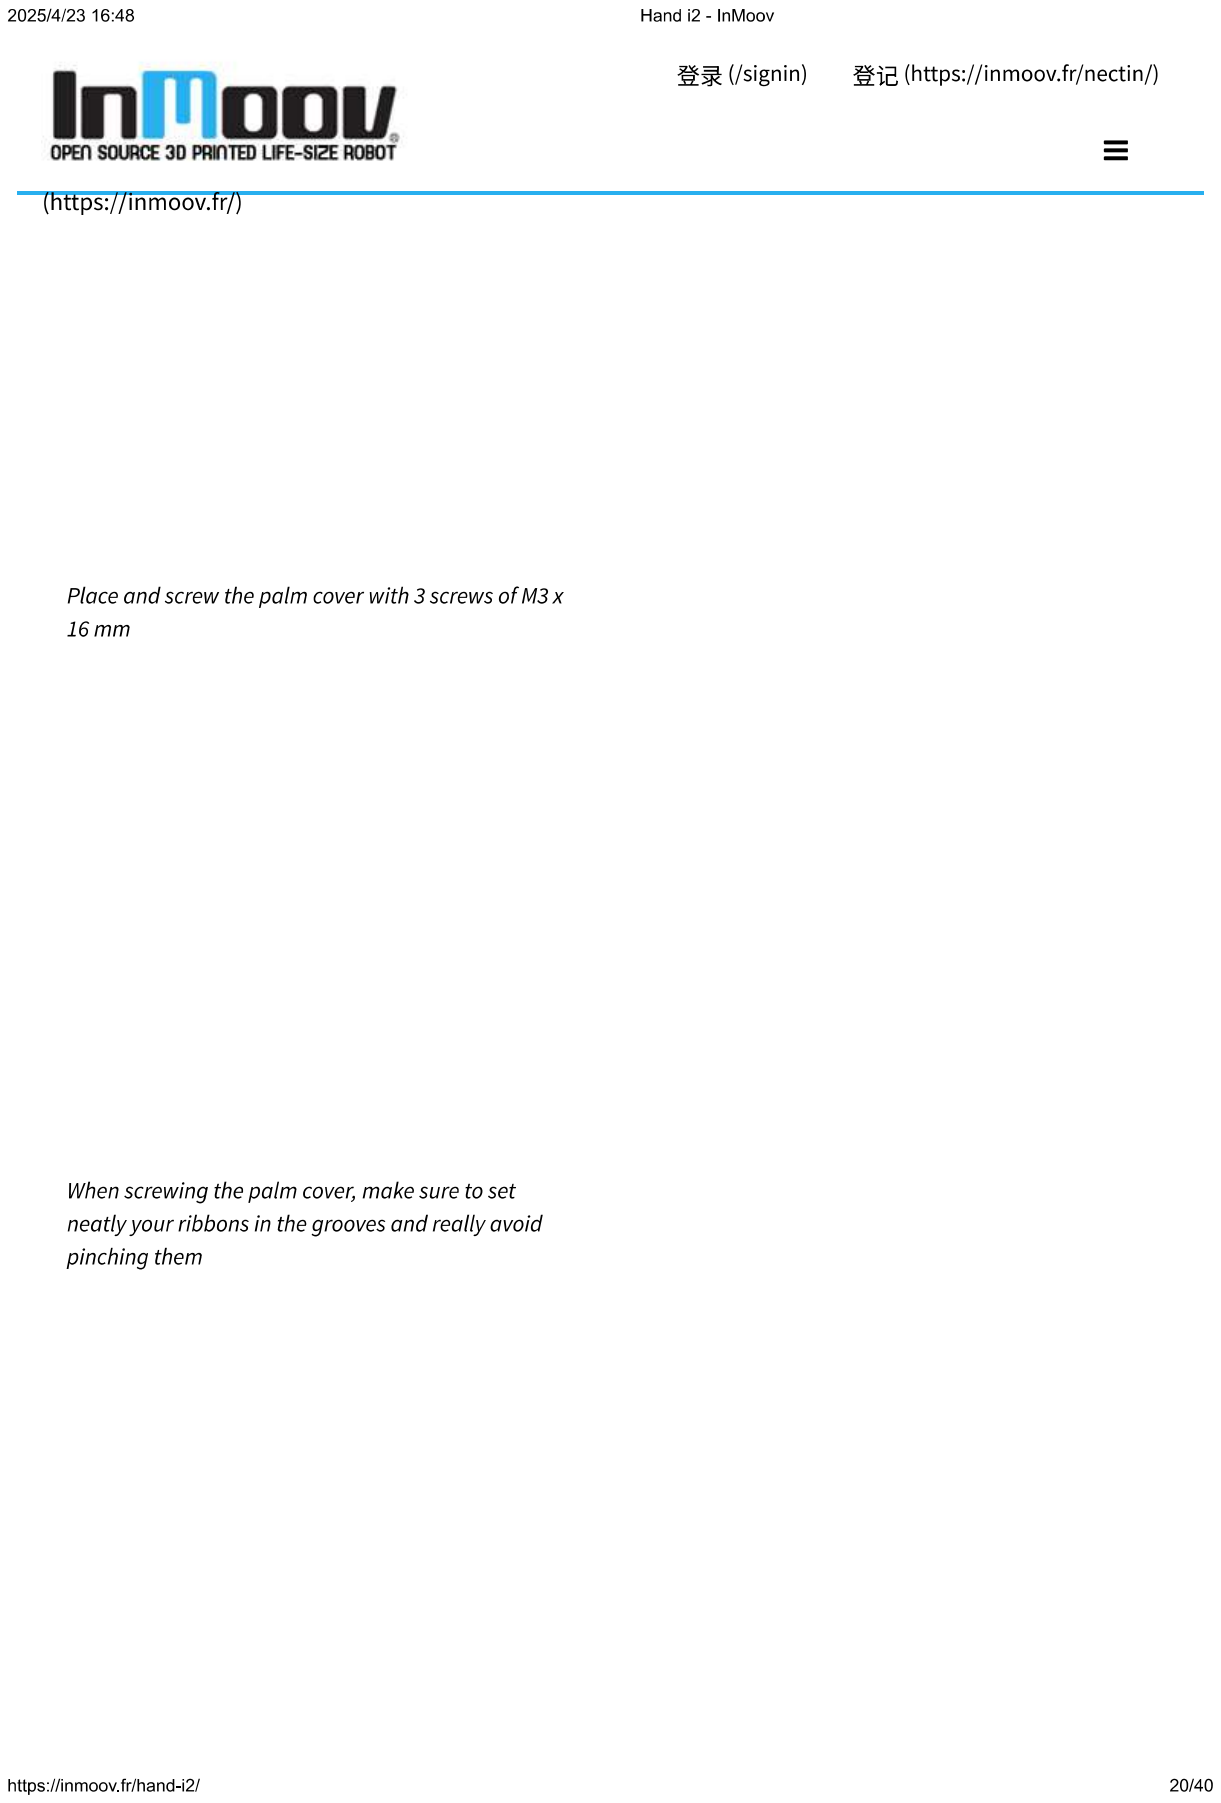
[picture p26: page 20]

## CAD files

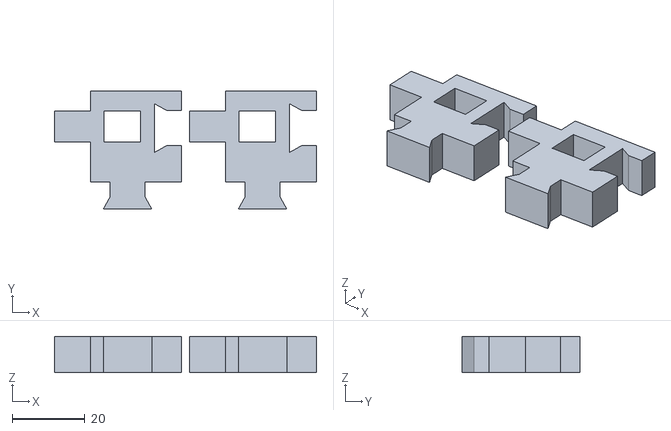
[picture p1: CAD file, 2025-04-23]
手部STL/Calibrator.stl
72.2 x 32.5 x 9.99

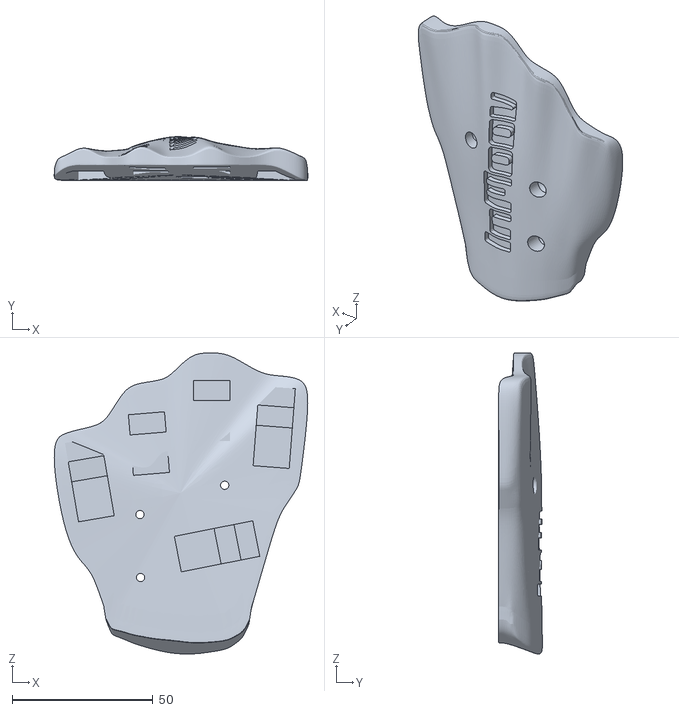
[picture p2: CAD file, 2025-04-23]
手部STL/右手/i2_HandPDI6225V2.stl
90.2 x 15.6 x 107.1

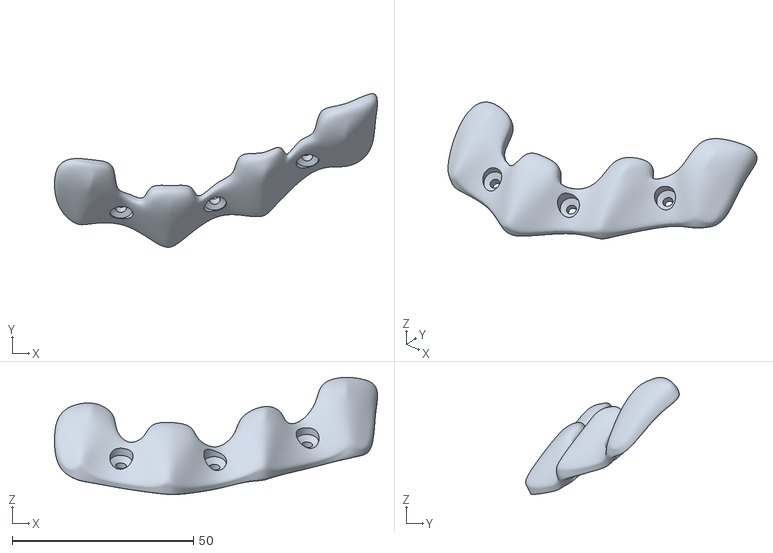
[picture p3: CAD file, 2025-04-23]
手部STL/左手/i2_LeftCoverFingerV3.stl
89.0 x 42.3 x 32.3

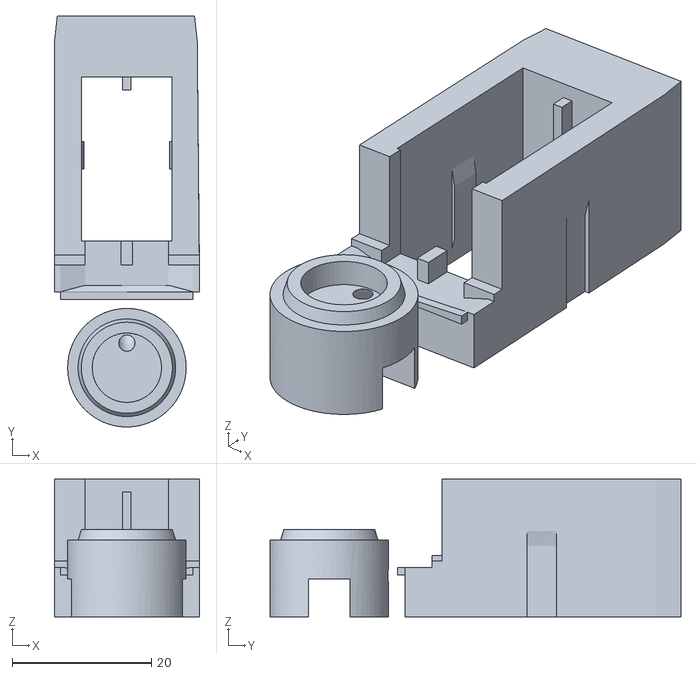
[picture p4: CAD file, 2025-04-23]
手部STL/右手/i2_Adapter1109MG.stl
20.8 x 58.9 x 19.8

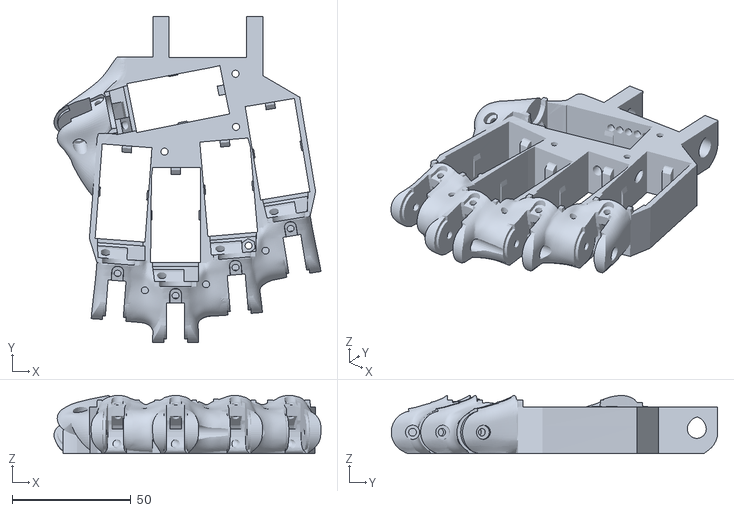
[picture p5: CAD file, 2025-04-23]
手部STL/左手/i2_LeftWristLargeV2.stl
112.6 x 137.7 x 24.5

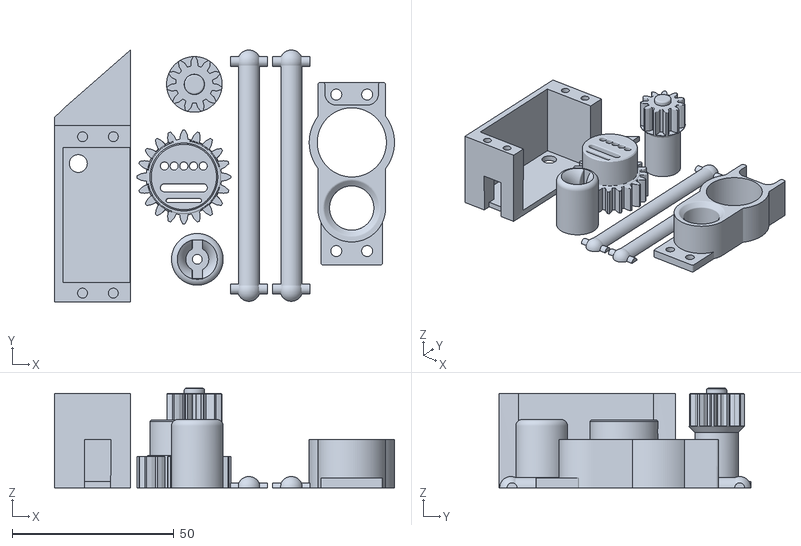
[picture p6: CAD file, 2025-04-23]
手部STL/右手/i2_WristGearV1.stl
105.2 x 78.1 x 30.8

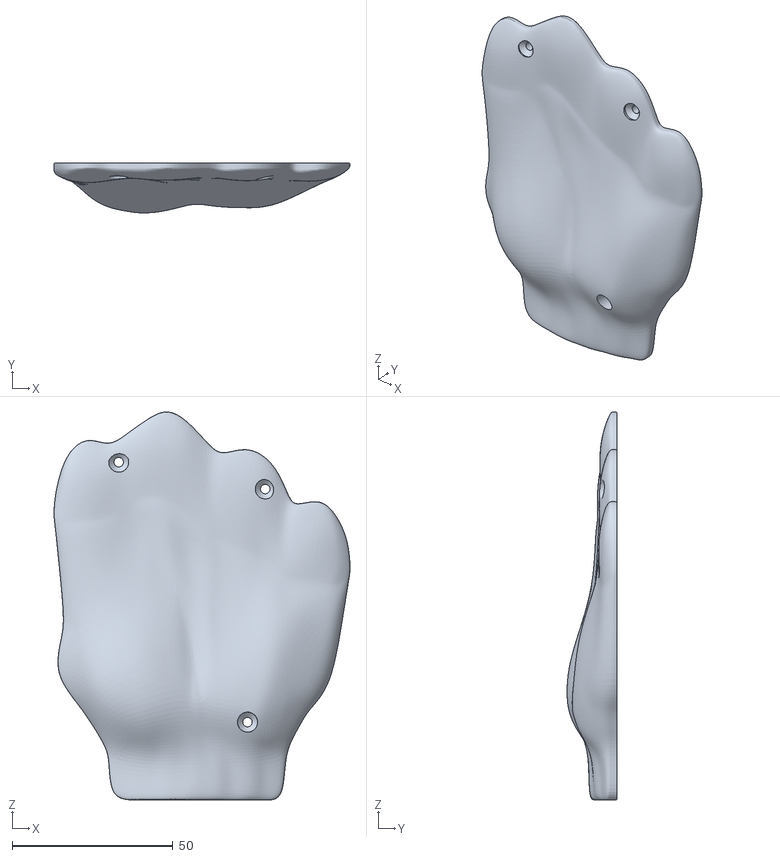
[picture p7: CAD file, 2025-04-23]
手部STL/左手/i2_LeftPalmCoverV2.stl
92.0 x 15.5 x 120.7

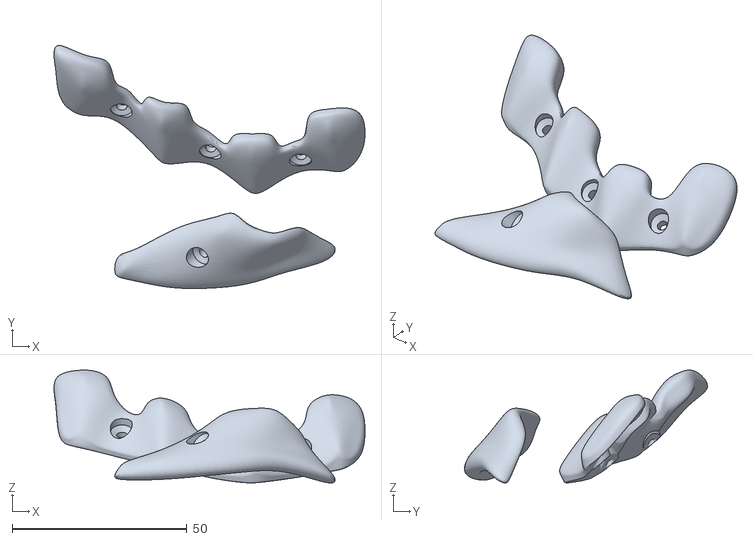
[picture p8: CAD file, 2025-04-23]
手部STL/右手/i2_CoverFingerV3.stl
89.0 x 69.6 x 32.3

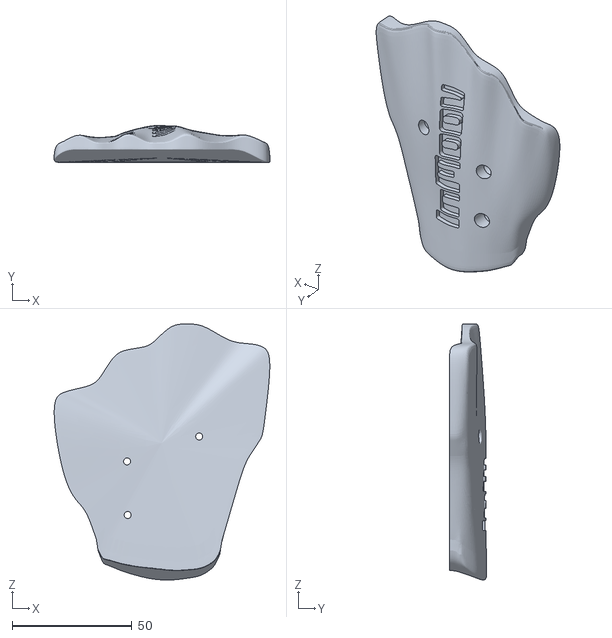
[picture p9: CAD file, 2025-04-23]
手部STL/右手/i2_HandCoverV1.stl
90.2 x 15.6 x 107.1

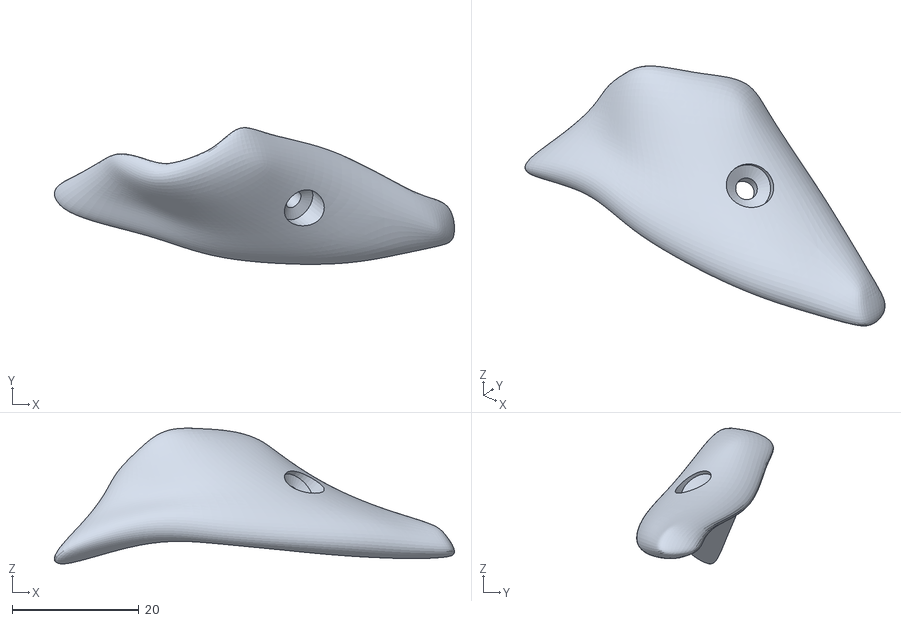
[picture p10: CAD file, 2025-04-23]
手部STL/左手/i2_LeftCoverThumbV3.stl
63.1 x 21.6 x 21.4

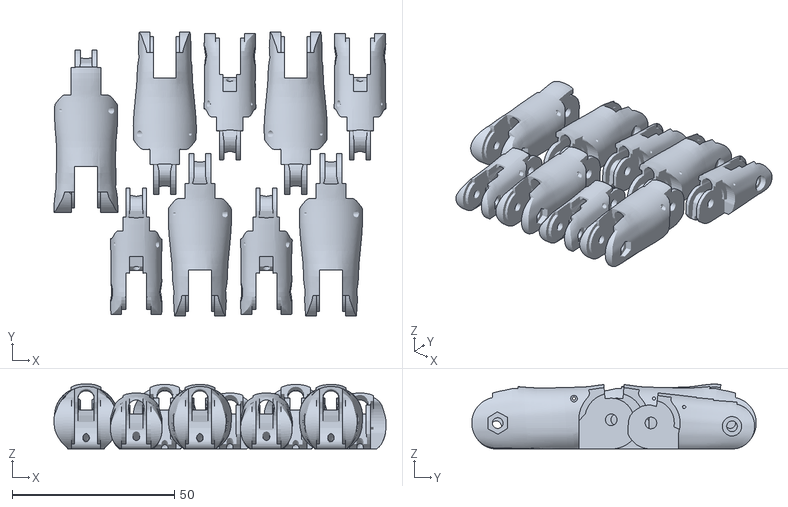
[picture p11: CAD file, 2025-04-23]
手部STL/右手/i2_FingersX5V2.stl
102.3 x 87.7 x 20.0

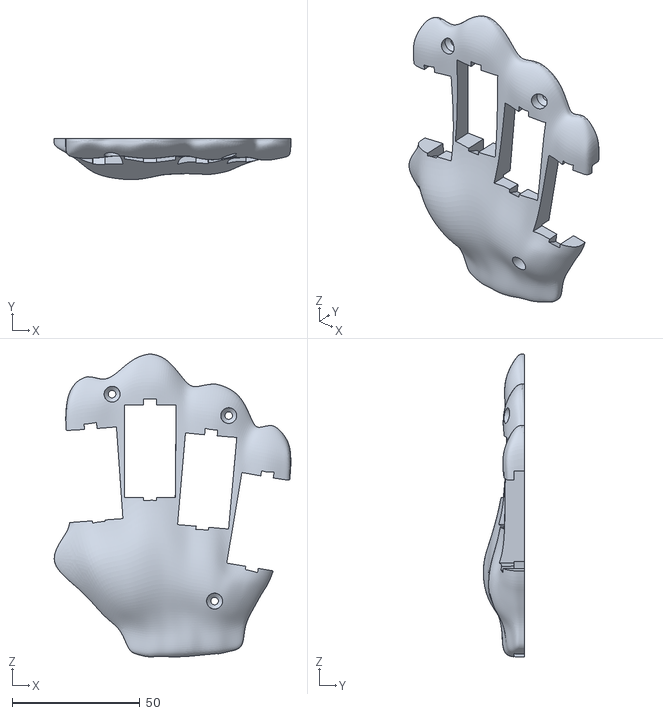
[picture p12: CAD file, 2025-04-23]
手部STL/左手/i2_LeftPalmPDI6225V3.stl
92.4 x 16.2 x 118.4

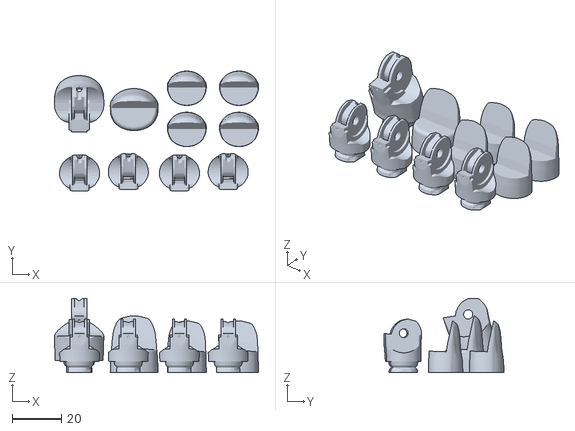
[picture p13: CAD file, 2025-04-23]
手部STL/右手/i2_FingersTipX5V2.stl
82.9 x 48.7 x 30.2

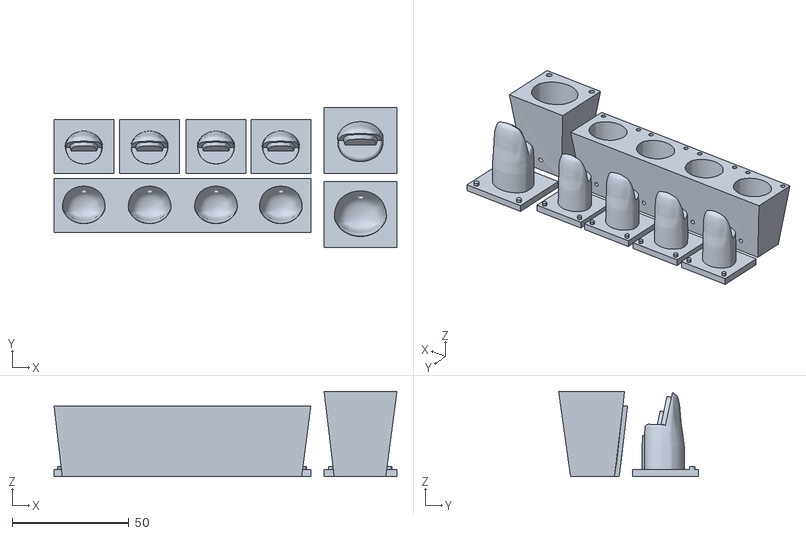
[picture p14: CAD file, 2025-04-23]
手部STL/右手/i2_FingersMoldX5V3.stl
146.8 x 59.8 x 36.5

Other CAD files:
手部STL/左手/i2_LeftHandPDI6225V2.stl
手部STL/右手/i2_WristLargeV2.stl
手部STL/左手/i2_LeftHandCoverV1.stl
手部STL/右手/i2_PalmCoverV2.stl
手部STL/右手/i2_PalmPDI6225V3.stl
手部STL/右手/i2_PulleyX5V1.stl
手部STL/左手/i2_LeftWristGearV1.stl
